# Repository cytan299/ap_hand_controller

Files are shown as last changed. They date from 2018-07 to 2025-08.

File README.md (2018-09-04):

# A simple hand controller for Astro-Physics mounts

by C.Y. Tan 2018

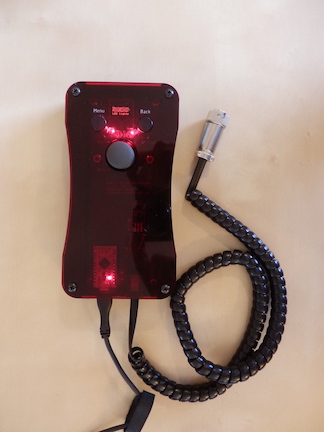
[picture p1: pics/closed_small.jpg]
Simple Astro-Physics Hand controller


It is well-known, that the new GTOCP4 control box can be controlled
with a phone or a pad. However, I really like the feel of real buttons
in a controller rather than using "virtual" buttons on a phone or pad.
This means that the only solution that Astro-Physics (AP) has for people like
me is to buy their AP keypad.

If I had the AP keypad, I will mainly use it for Polar aligning with
PoleMaster and for recalibrating (which is the same as syncing for all
other mounts). After polar alignment and recalibrating, PHD2 will be
used for guiding the scope. Therefore, the AP keypad will only be used
at the start of my imaging session, and no more. Thus, it is hard for
me to justify spending $1000 for an AP keypad when I will hardly use.
I had to figure out a solution.

And here's my solution:
* I have built a simple hand controller for my Mach1GTO. Its purpose
is **not** to replace the AP keypad because it does not initialize the
CP4, have any star database or goto capability etc. My goal is to just
move the mount for calibrating the mount to a star and be compatible
with PoleMaster.

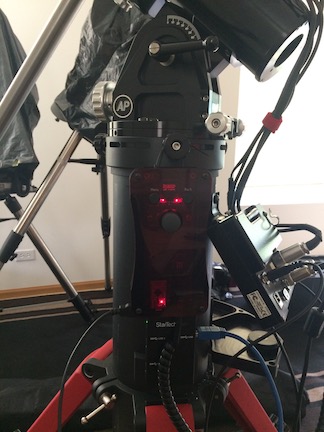
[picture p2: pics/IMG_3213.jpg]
Hand controller connected to the GTOCP4


## Design

The goal of my hand controller is to be low cost (less than $200). The
simplest way I know how to do this is to base it on an
[Arduino controller](https://www.sparkfun.com/products/12640). The
other low cost components are

* A small 64x48
  [OLED display](https://www.ebay.com/itm/0-66-OLED-Display-Module-7pin-64x48-Screen-SPI-I2C-3-3-5V-for-Arduino-AVR-STM32/311968961516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)
  for showing the user options and the state of the controller.
* A [thumb joystick](https://www.sparkfun.com/products/9032) for
selecting menu items and for moving the telescope in RA and DEC.
* The hand controller will be connected to the same port that the AP
  keypad uses. 

## Support

This is unsupported hardware. Build at your own peril! :)

You can submit questions or bug reports using the
[issues](https://github.com/cytan299/ap_hand_controller/issues) tab on
the right and then click on **NEW**.

Have fun!

## Directory structure

* **howto** Assembly instructions for the hand controller.
* **ponoko** The files that are used for laser cutting the acrylic parts of
the design. These files can be sent directly to
[Ponoko](http://www.ponoko.com) for laser cutting.
* **bom** Bill of materials for one hand controller.
* **eagle** Eagle schematic and board files.
* **arduino** Source code for the hand controller.
* **pics** Photographs used in the README's and Wiki.
* **user manual** contains the hand controller user manual.

## Other information

More information can be found in he *README.md* files in each
directory and the [wiki](https://github.com/cytan299/ap_hand_controller/wiki/A-simple-hand-controller-for-Astro-Physics-mounts) of this project on github.

## Copyright
All the software, documentation, and hardware that I have written is
copyright 2018 C.Y. Tan.

All software is released under GPLv3

All documentation is released under:
* Creative Commons Attribution-ShareAlike 3.0 Unported License
* GNU Free Documentation License, Version 1.3
* Creative Commons Attribution-ShareAlike 4.0 International License

All hardware is released under CERN Hardware Open License v1.2

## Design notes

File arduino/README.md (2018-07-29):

# Arduino source code

This directory contains the arduino source code for the hand
controller. The code has been successfully compiled using
ARDUINO 1.8.5.

## Directories

* **hand_controller** This contains the *hand_controller.ino* file
which is the entry point for the controller program.
* **lib** This contains the libraries which are required for compiling
  *hand_controller.ino*. The README.md file contains more information about
  these libraries.

## Copyright

The software that is written by the author is copyright 2018 C.Y. Tan
and released under GPLv3.

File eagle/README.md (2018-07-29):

# Eagle files

These are the eagle files that can be sent to pc board manufacturers to
be made. There is a free version of [eagle](http://cadsoftusa.com)
that can be downloaded to view the designs.

## Directories

* **ap_hand_controller** The hand controller unit schematic and pcb.

## Copyright

The schematic and board designs are copyright 2018 C.Y. Tan and
released under the CERN Open Hardware License v1.2

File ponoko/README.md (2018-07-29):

# Hand controller box and front cover

The hand controller box case and front cover are in this directory. Note that
the svg files are *not* empty! The lines are 0.01 mm thick that are
required for laser cutting by [Ponoko](http://www.ponoko.com). To see
the designs, either zoom in or change the thickness of the lines with
a programme like [Inkscape](https://inkscape.org/en/).

* *ponoko_hc_box_v2.svg* contains enough parts for one hand controller box
and spacers for mounting the pcb into the box. If you use the _red
tint_ acrylic material for this part then you do not need to make a
red, transparent front cover. In my prototype, I had used acrylic
black for the body and
because it is not transparent, I had to make a separate front cover in
red tint. The specified material used for manufacture at [Ponoko](http://www.ponoko.com) is
  * Acrylic red tint or black
  * 3.0 mm thick
  * P2 - 384.0 mm long x 384.0 mm wide
* *ponoko_cover.svg*  is _optional_. It contains the design for the front cover of the
  box.The material used must be red and transparent, i.e.
  * Acrylic red tint
  * 3 mm thick
  * P1 - 181.0 mm long x 181.0 mm wide

## Copyright

The hand controller box and front cover designs are copyright 2018 C.Y. Tan and released under the CERN Open Hardware License v1.2

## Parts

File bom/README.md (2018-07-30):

# Bill of Materials

The estimated cost for building *one* hand controller is about $150.
Taxes and shipping have not been included. This is the lower bound for
the cost of one such device because, in practise, it is not possible
to just buy 1 screw.  The bom.ods file is readable using
[LibreOffice Calc](http://www.libreoffice.org).

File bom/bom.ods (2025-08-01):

Part # | Description | Price each | # required | Cost of 1 | Bought from | Total cost of 1
COM-00589 | RS232 converter SMD | $1.95 | 1 | $1.95 | www.sparkfun.com | $156.86
COM-09032 | Thumb Joystick | $3.95 | 1 | $3.95
COM-10302 | Tactile Button Assortment | $0.50 | 2 | $0.99
DEV-12587 | Pro Micro - 3.3V/8MHz | $19.95 | 1 | $19.95
PRT-00132 | RJ11 6-Pin Connector | $1.25 | 1 | $1.25
ROB-13134 | Standoff 6-32, 1” | $0.62 | 4 | $2.49
450-1661-ND | Tactile switch right angled | $0.18 | 1 | $0.18 | www.digikey.com
945-1661-5-ND | R-78E3.3-0.5 DC/DC converter 3.3V | $2.70 | 1 | $2.70
HR1732-ND | Connector plus male 5 position | $13.49 | 1 | $13.49
A3662R-05C-ND | Cable mod 6P6C plug cable 5 ft | $3.13 | 1 | $3.13
160-1169-1-ND | LED green 1206 SMD | $0.25 | 1 | $0.25
160-1406-1-ND | LED yellow 1206 SMD | $0.28 | 1 | $0.28
 | PCBs | $22.00 | 1 | $22.00 | www.oshpark.com
10792 | 64x48 0.66” OLED white display module | $4.90 | 1 | $4.90 | https://www.buydisplay.com/serial-spi-i2c-white-0-66-inch-arduino-raspberry-pi-oled-display-64x48
331712 | Laser cut case | $59.30 | 1 | $59.30 | www.ponoko.com
99558 | 6-32 3/8” black pan head screws | $0.30 | 8 | $2.40 | www.homedepot.com
99388 | 4-40 1/2” black pan head screws | $0.29 | 6 | $1.74
887480021219 | 4-40 nuts | $0.10 | 6 | $0.59
 | Taxes | $0.56
C503B-RAN-CZ0C0AA2 | Red clear 5 mm round LED | $0.15 | 2 | $0.30 | www.digikey.com
RHM100AHTR-ND | 0805 surface mount 100 ohm resistor | $0.36 | 2 | $0.72
732-8086-2-ND | 1206 surface mount 0.1 uF ceramic capacitor | $0.10 | 5 | $0.50
1189-4041-ND | Radial electrolytic capacitor 10uF, 50V | $0.28 | 2 | $0.56
10.0KXBK-ND | 10 kohm resistor, ¼ W | $0.10 | 4 | $0.40
49.9XBK-ND | 50 ohm, ¼ W | $0.10 | 1 | $0.10
ED3024-ND | 24 pin IC socket | $1.12 | 1 | $1.12
ED4624-ND | 24 pin IC wirewrap socket | $4.66 | 1 | $4.66
3008 | 36-pin 0.1” short female header | $1.60 | 0.194 | $0.31 | www.adafruit.com
MMPin-40 | 40 pin SIP header strip | $2.66 | 1 | $2.66 | www.solarbotics.com
 | Olympus adjustable wrist wrap | $3.99 | 1 | $3.99 | https://www.amazon.com/gp/product/B001TKYMTA/ref=oh_aui_detailpage_o00_s00?ie=UTF8&psc=1

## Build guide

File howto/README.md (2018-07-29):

# How to build the AP hand controller

I have written one document to help you build and assemble my AP hand controller

## The documents

* **assembly.pdf** This guide tells you how I assembled the
  parts of hand controller.

## Copyright

These documents are copyright 2018 C.Y. Tan and released under
Creative Commons Attribution-ShareAlike 3.0 Unported License.

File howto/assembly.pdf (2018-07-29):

# AP handcontroller assembly instructions

## C.Y. Tan

7/29/18

2 | AP Handcontroller | 7/29/18

# License

## Copyright 2018 C.Y. Tan This document is licensed under Creative Commons Attribution-ShareAlike 3.0 Unported License. To view a copy of this license, visit http://creativecommons.org/licenses/by-sa/3.0/

3 | AP Handcontroller | 7/29/18

# Assembly instructions

## - These instructions will only highlight the important parts of the

assembly.

### - The assembly is quite straightforward, but as usual, there are some parts of

the assembly that need a little bit of care and feeding.
- All the required parts are listed in the bill of materials.

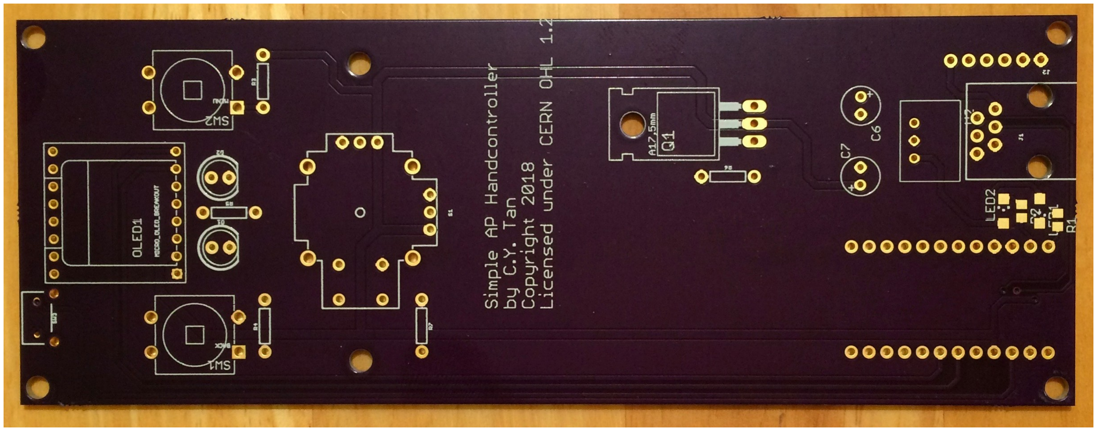
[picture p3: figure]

4 | AP Handcontroller | 7/29/18

# Electronics

This is the prototype printed circuit board that I’ll be using to demonstrate how to assemble the hand controller.

The version 2 hand controller that is on the github site is nearly the same as the prototype. The obvious part that is missing in version 2 of the hand controller is the MOSFET.

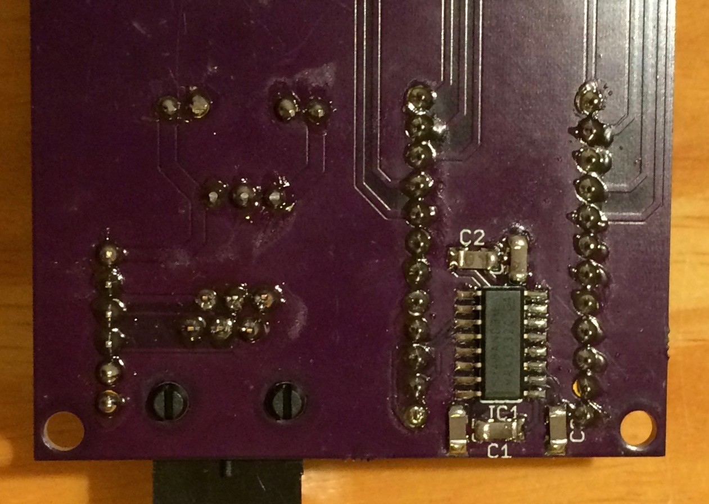
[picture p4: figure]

5 | AP Handcontroller | 7/29/18

# Surface mount parts

There are surface mount parts that need to be soldered at the back of the printed circuit board.

These parts are for the RS232 level shifters. They are actually very easy to solder to the pads with thin solder (0.8 mm diameter, 60/40 solder) and a soldering iron with a fine tip.

However, if you’ve never soldered before, it’s best to ask a friend who is an experienced at soldering electronics to do it.

# Making the pushbuttons

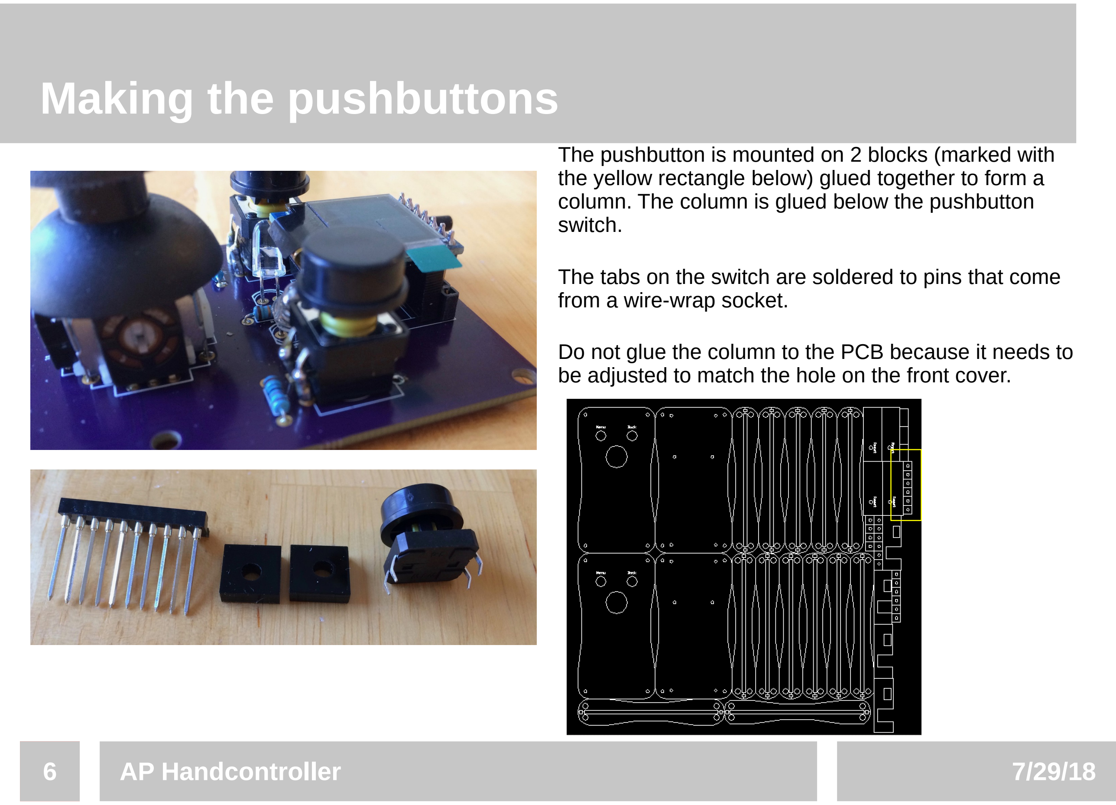
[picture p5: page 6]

6 | AP Handcontroller | 7/29/18

The pushbutton is mounted on 2 blocks (marked with the yellow rectangle below) glued together to form a column. The column is glued below the pushbutton switch.

The tabs on the switch are soldered to pins that come from a wire-wrap socket.

Do not glue the column to the PCB because it needs to be adjusted to match the hole on the front cover.

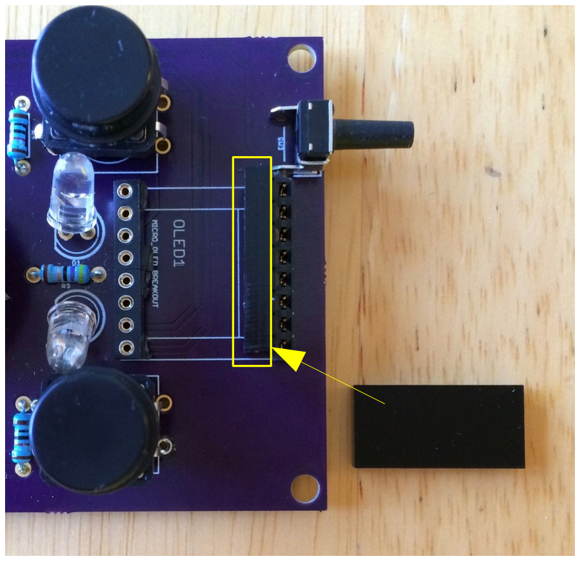
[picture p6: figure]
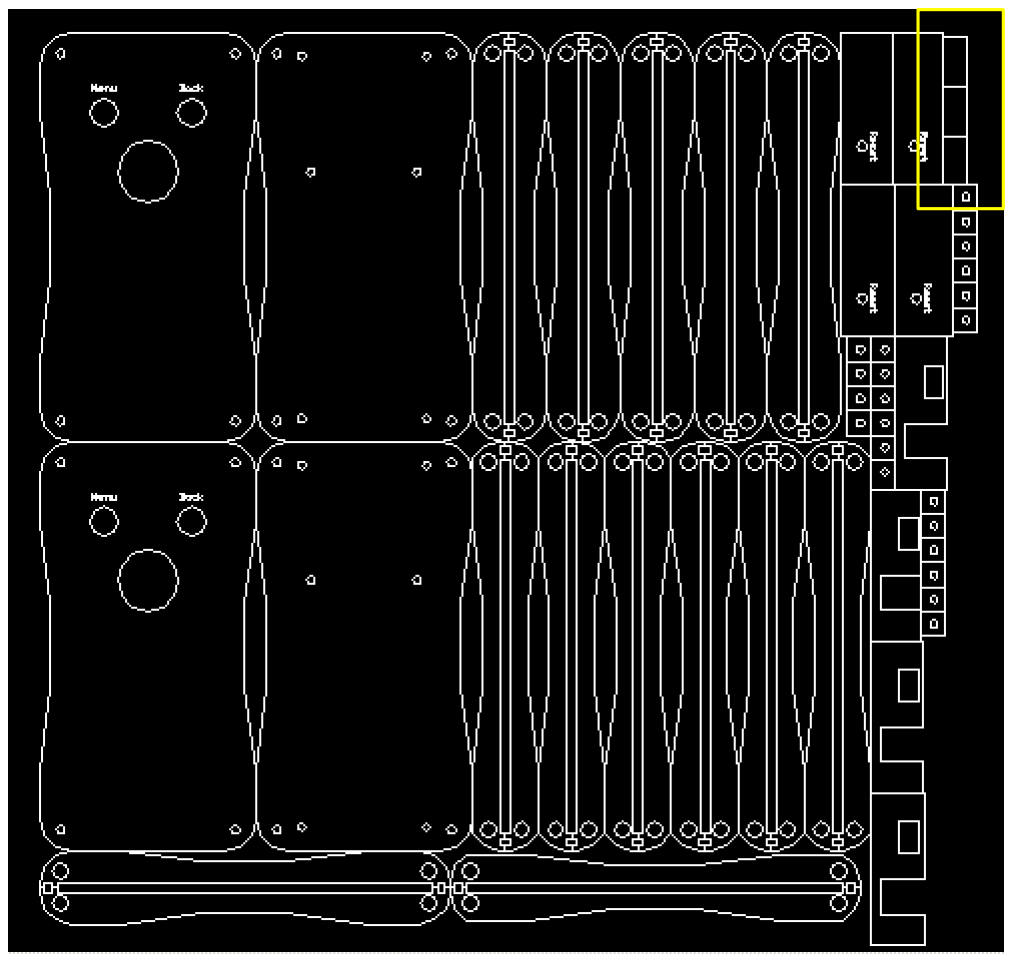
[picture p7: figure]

7 | AP Handcontroller | 7/29/18

# Supporting the OLED

The OLED module only has pins on one side and so it flops after installation into its socket. There are blocks (marked in a yellow rectangle in the right figure) that can be used to prop up the OLED. The block is simply glued to the PCB.

Note: The above PCB is the prototype version. Version 2 has the OLED socket nearest to the LEDs.

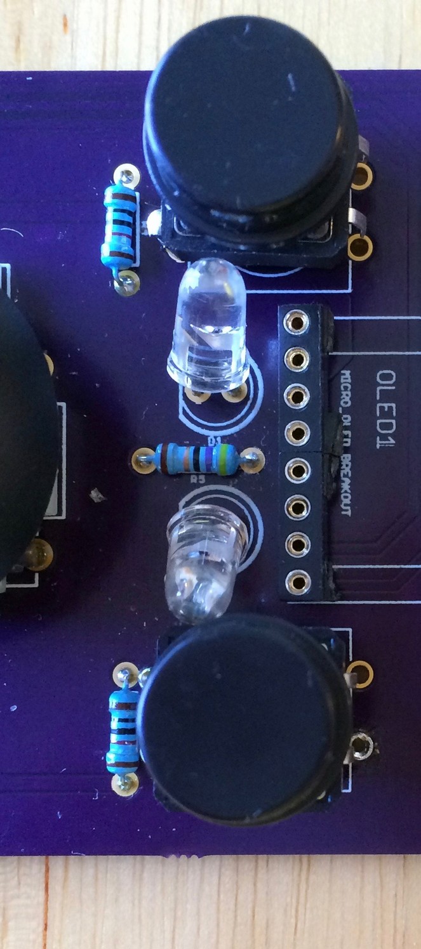
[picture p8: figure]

8 | AP Handcontroller | 7/29/18

# Installation of LEDs

The LEDs are used to light up the switches so that they can be seen in the dark.

They are bent towards the switches and should be installed last.

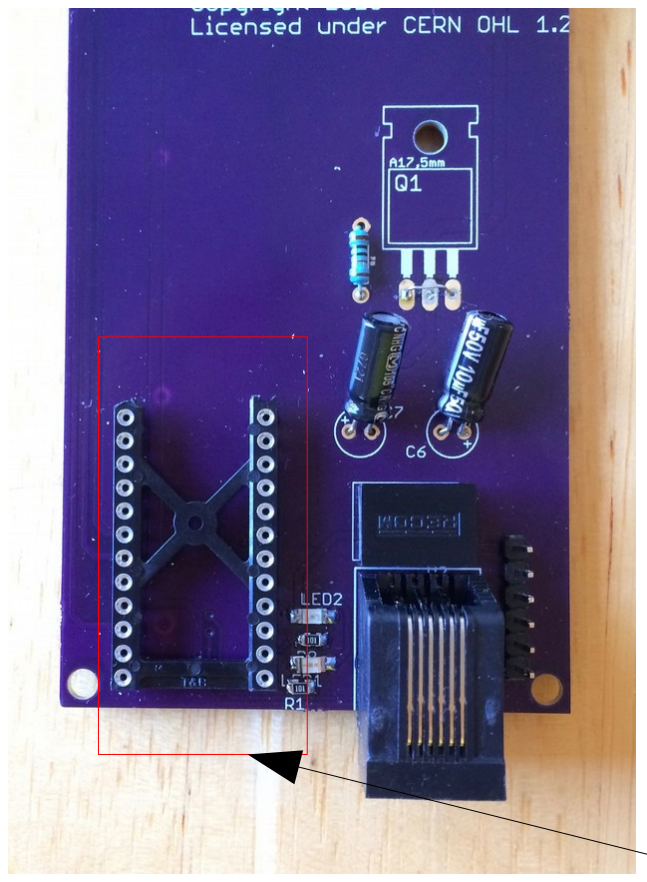
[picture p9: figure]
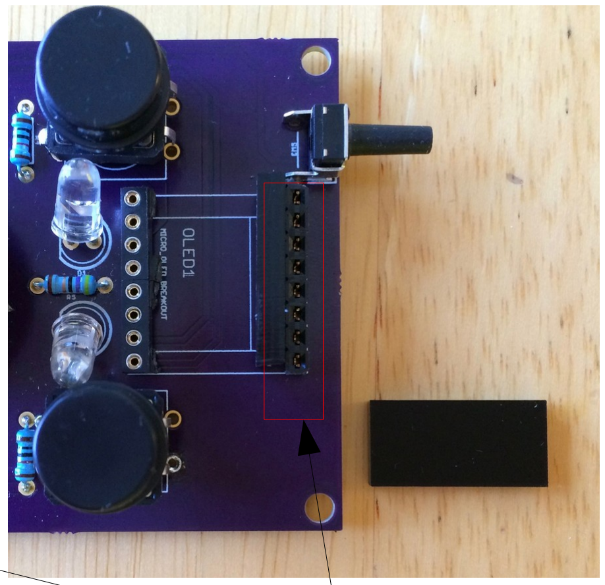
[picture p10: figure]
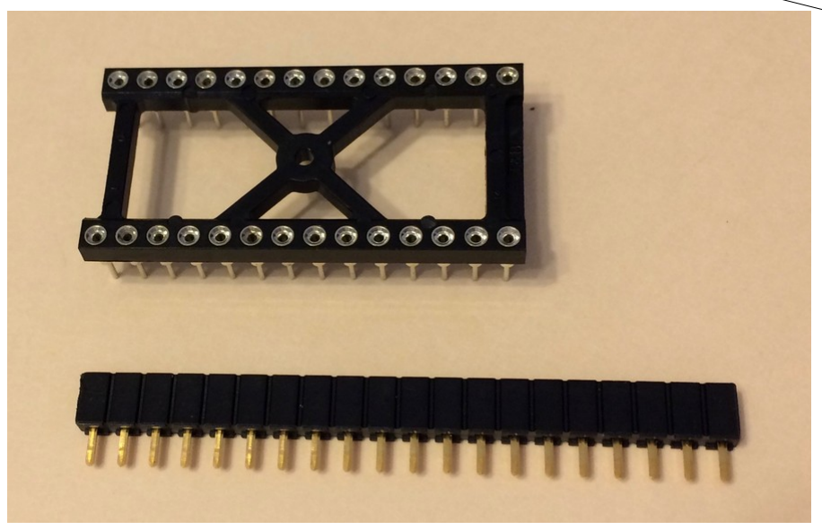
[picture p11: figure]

9 | AP Handcontroller | 7/29/18

# Populating the PCB

Populate the lowest height components first. Start with surface mount parts, and then resistors, IC sockets, electroytic capacitors, switches, 6P6C connector and finally the joystick.

The assembly of the pushbuttons and LEDs are discussed in later slides.

Sockets are used for the Arduino and the OLED display.

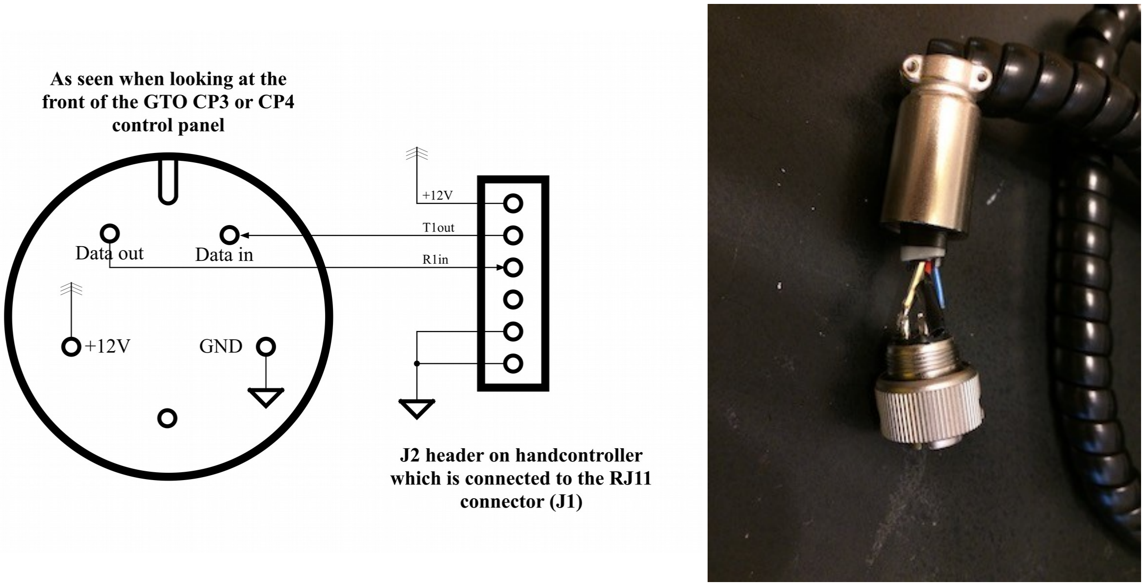
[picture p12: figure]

10 | AP Handcontroller | 7/29/18

# Making the AP keypad connector

There are 6 wires but only 5 wires are soldered to the connector. The 2 GND wires are soldered to the same pin.
One of the extra wires is just covered with insulating tape.

# Making the case

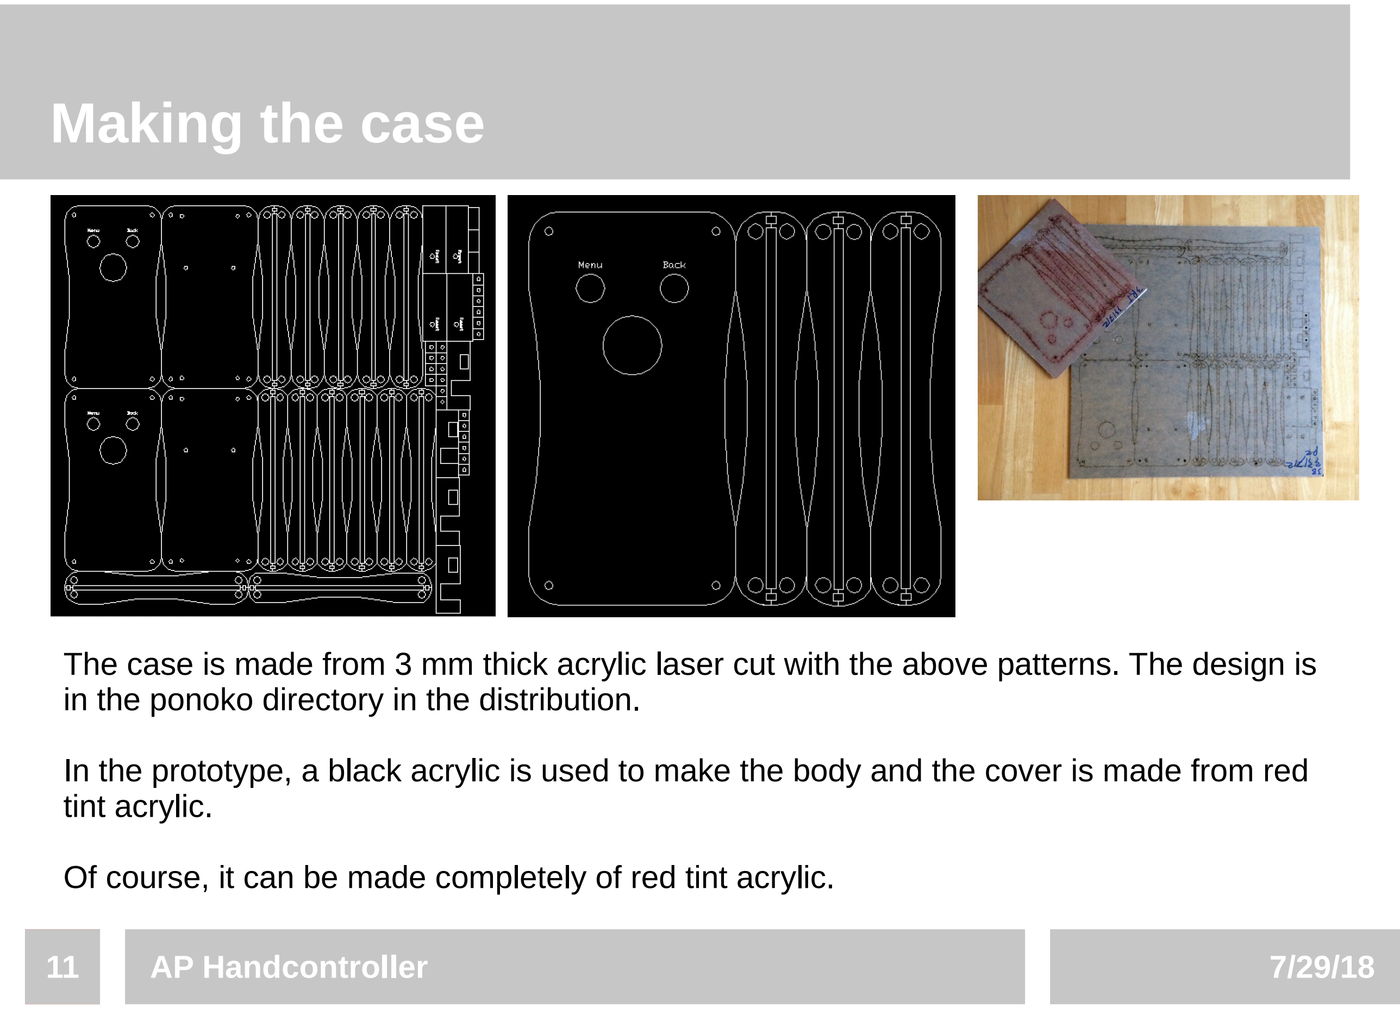
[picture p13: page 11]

11 | AP Handcontroller | 7/29/18

The case is made from 3 mm thick acrylic laser cut with the above patterns. The design is in the ponoko directory in the distribution.

In the prototype, a black acrylic is used to make the body and the cover is made from red tint acrylic.

Of course, it can be made completely of red tint acrylic.

# Stacking the case

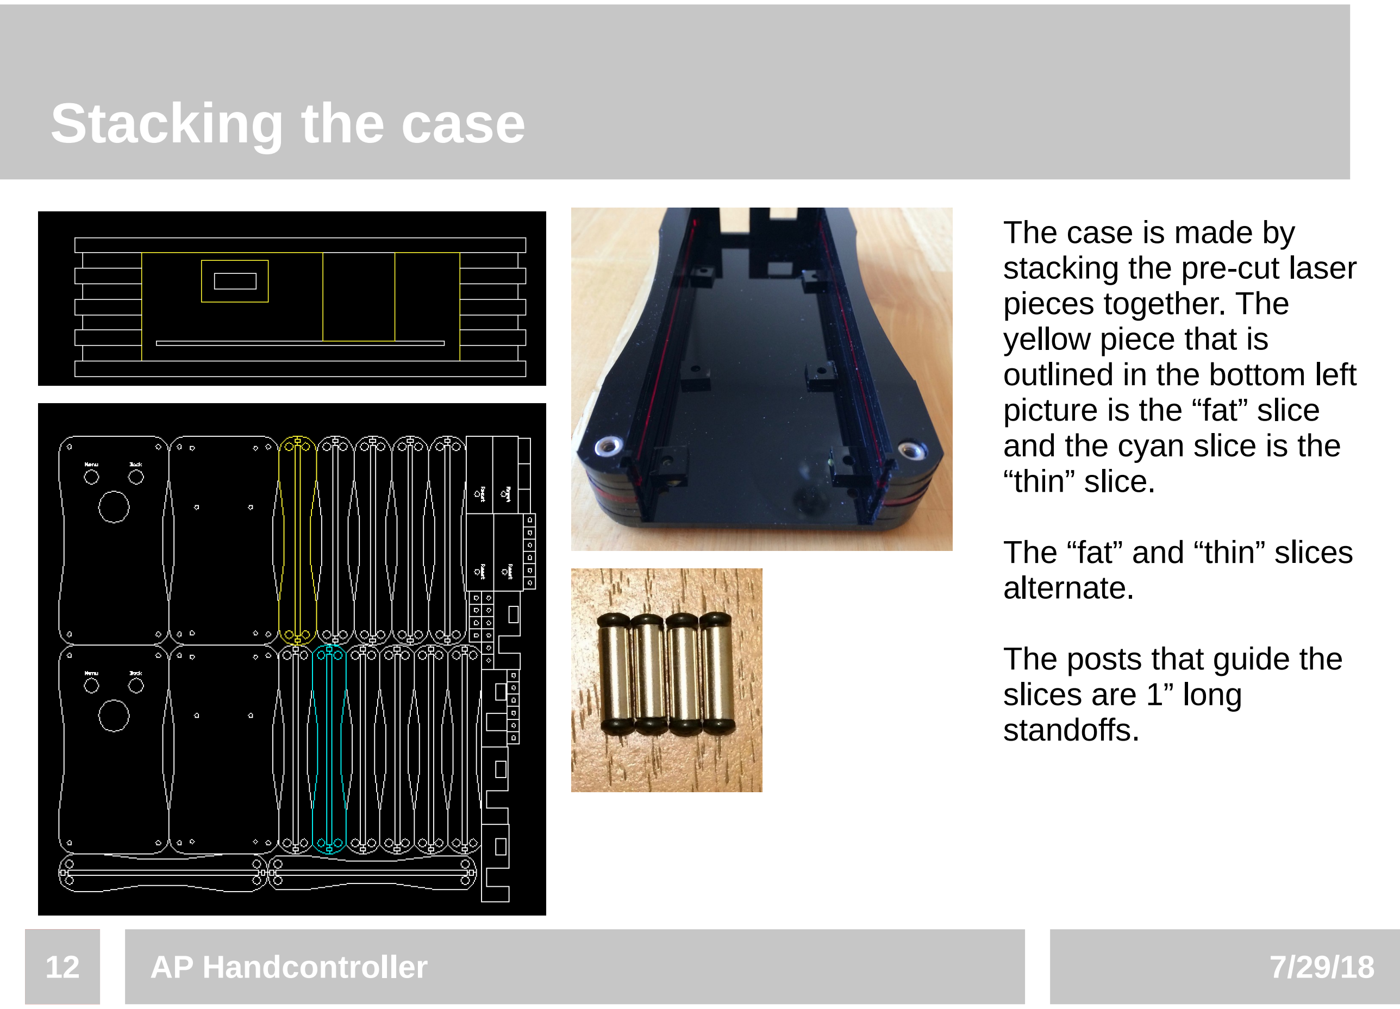
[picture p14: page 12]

12 | AP Handcontroller | 7/29/18

The case is made by
stacking the pre-cut laser pieces together. The
yellow piece that is
outlined in the bottom left picture is the “fat” slice and the cyan slice is the
“thin” slice.

The “fat” and “thin” slices alternate.

The posts that guide the
slices are 1” long
standoffs.

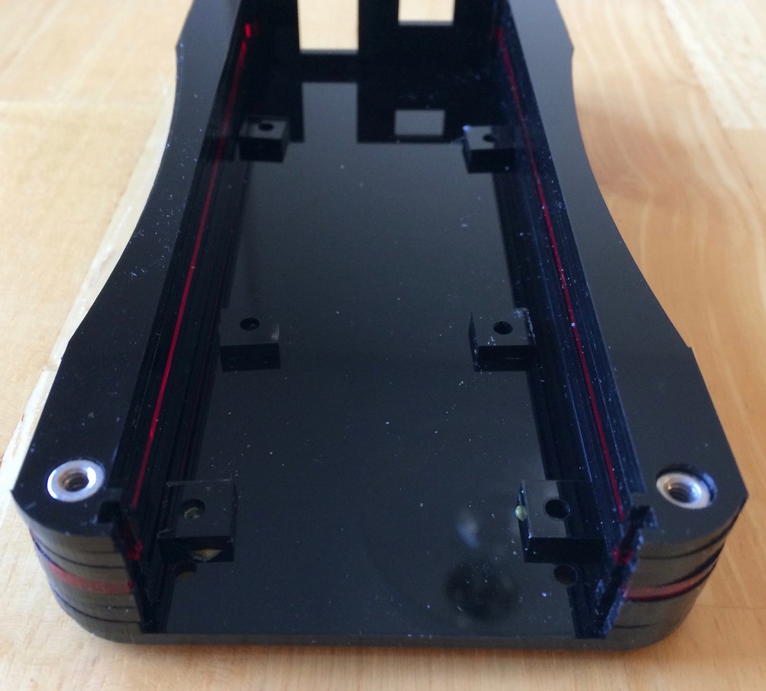
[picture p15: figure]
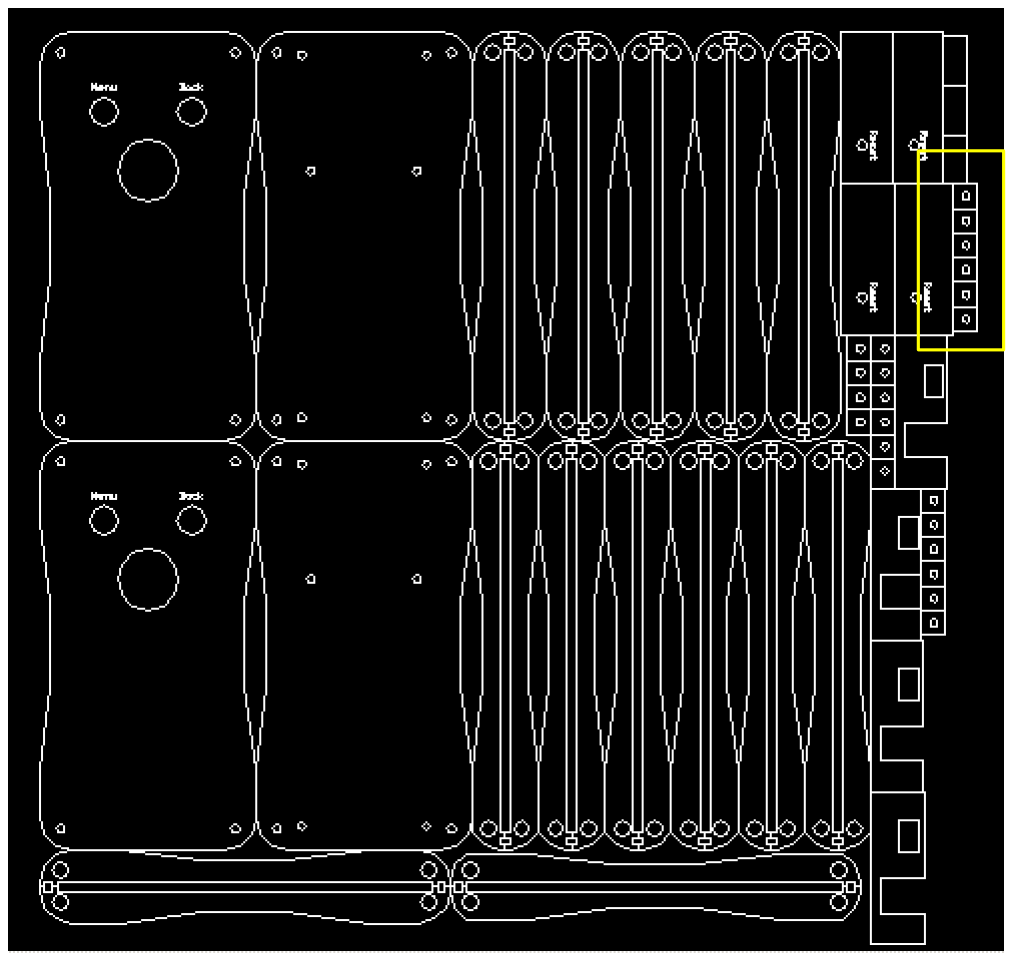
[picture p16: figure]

13 | AP Handcontroller | 7/29/18

# Gluing in standoffs

The blocks that are used to make standoffs are in the yellow rectangle in the right figure. They are glued to the bottom of the case.

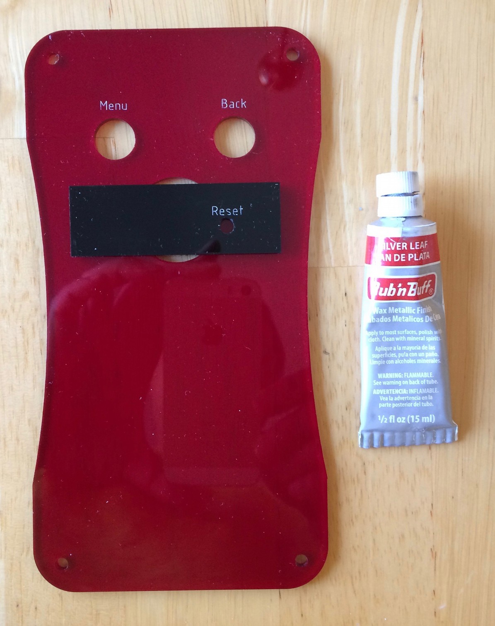
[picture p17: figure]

14 | AP Handcontroller | 7/29/18

# Highlighting marks

The laser engraved characters are highlighted by rubbing in silver Rub’N’Buff compound.

The excess is wiped off using ethanol.

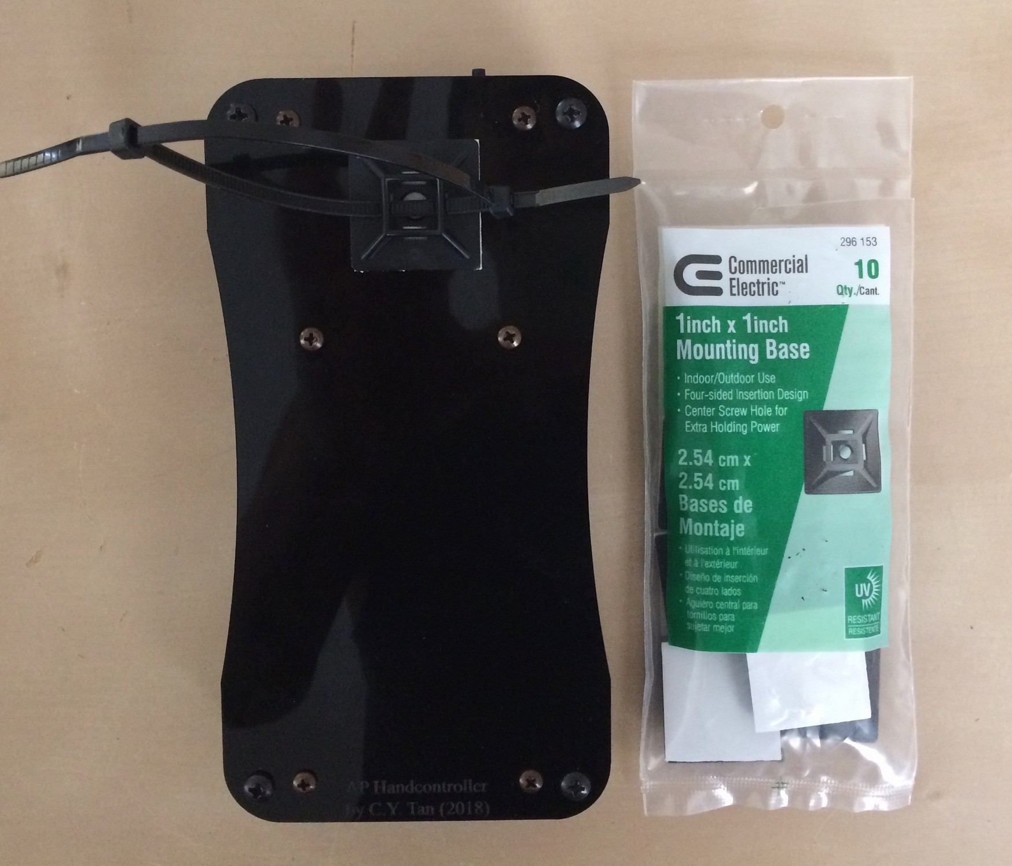
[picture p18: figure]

15 | AP Handcontroller | 7/29/18

# Hanging loop for the controller

I made a hanging loop for the controller using cable ties looped through a cable tie mounting base.

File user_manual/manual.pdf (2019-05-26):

# A Simple Hand Controller for Astro-Physics

Mounts Operating Manual by C.Y. Tan (26.

# May. 2019)

## 1 License

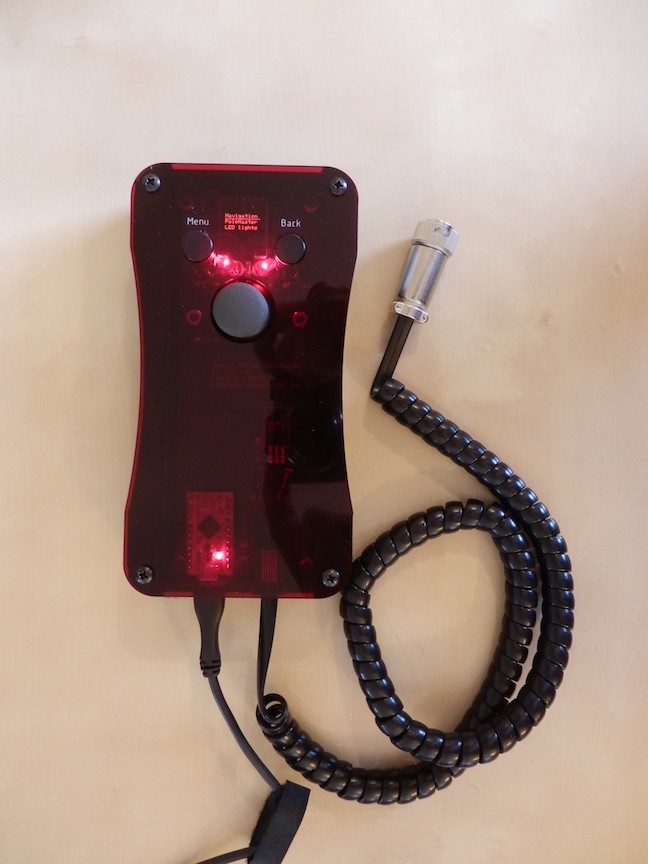
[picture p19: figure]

This work is licensed under the Creative Commons Attribution-ShareAlike 4.0 International License. To view a copy of this license, visit http://creativecommons.org/licenses/by-sa/4.0/ or send a letter to Creative Commons, PO Box 1866, Mountain View, CA 94042, USA.

## 2 Introduction

It is well-known, that the new GTOCP4 control box can be controlled with a phone or a pad. However, I really like the feel of real buttons in a controller rather than using “virtual” buttons on a phone or pad. This means that the only solution that Astro-Physics (AP) has for people like me is to buy their AP keypad.

If I had the AP keypad, I will mainly use it for Polar aligning with PoleMaster (lately with SharpCap

A Simple Hand Controller for Astro-Physics Mounts Operating Manual | 1

Pro as well) and for recalibrating (which is the same as syncing for all other mounts). After polar alignment and recalibrating, PHD2 will be used for guiding the scope. Therefore, the AP keypad will only be used at the start of my imaging session, and no more. Thus, it is hard for me to justify spending $1000 for an AP keypad which I will hardly use.

I had to figure out a solution.

And here's my solution:
- I have built a simple hand controller for my Mach1GTO. Its purpose is not to replace the AP keypad because it does not initialize the GTOCP4, have any star database or goto capability etc. My goal is to just move the mount for calibrating the mount to a star and be compatible with PoleMaster.

## 3 The hand controller hardware guide

The hand controller plugs into the GTOCP3 or GTOCP4 keypad port.

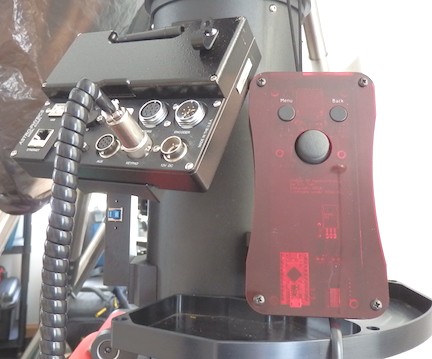
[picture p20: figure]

The hand controller does NOT have the RECAL option. This is a deliberate design decision. This is so that there will never be any confusion about which device will RECAL – it will always be the computer that is connected to the mount.

## 3.1 The buttons and joystick action guide

The actions associated with the buttons and joystick are defined in the table shown below. The shortcuts for that are used in this manual are also defined here.

A Simple Hand Controller for Astro-Physics Mounts Operating Manual | 2

Button | Description | Shortcut
Menu | When pressed, the hand controller goes back to the main menu. It also
| stops the mount from slewing. | MENU
Back | When pressed, the hand controller goes back to the previous menu. It
| also stops the mount from slewing. | BACK
Reset | Resets the hand controller. | RESET
Joystick UP/DOWN | In the menu environment, UP/DOWN, moves the cursor up and down. In the navigation environment, UP/DOWN is mapped to North/South slews. | ⇧/⇩
Joystick LEFT/RIGHT | In the menu environment, LEFT/RIGHT acts like a swipe. RIGHT moves to the next selected submenu. LEFT goes back to the previous menu. In the navigation environment, LEFT/RIGHT is mapped to East/West slews. | ⇦ ⇨/
Joystick Button | In the menu environment, the joystick button acts like the return key. In the navigation environment, the joystick button cycles through the slew rates. | ◙

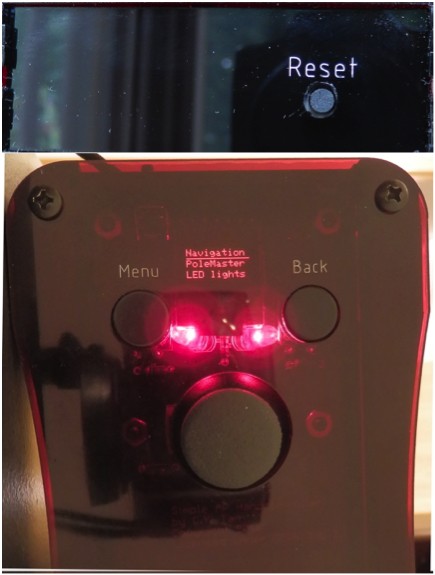
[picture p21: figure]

A Simple Hand Controller for Astro-Physics Mounts Operating Manual | 3

## 4 How to use

The hand controller can be connected to the GTOCP3 or GTOCP4 keypad port before power up. If it is
connected before power up, the controller has to be | RESET | before use. This is to establish a reliable
serial connection with the mount. IMPORTANT! The mount must be unparked (in APCC or the AP
ASCOM driver) and | RESET | must be pushed before use. If you use the hand controller before the
mount is unparked, the hand controller will still move the mount but POLEMASTER::SET HOME will be incorrect and thus POLEMASTER::GO HOME will send the mount to the wrong position.
Once powered up and | RESET | you can start using the hand controller.

## 4.1 Menu actions

Everything starts from the Main Menu.

Move through each menu item by ⇧/⇩,
and select it with ◙, or use . ⇨
In order to get back out of any control panel or submenu, just use | MENU | or use | BACK.
Pressing these buttons also stops the mount from moving. This is one way to stop the mount if anything goes wrong during a slew.
A Simple Hand Controller for Astro-Physics Mounts Operating Manual | 4

### 4.1.1 Navigation menu

Selecting Navigation brings up the Navigation submenu which has 3 submenu items.

Selecting the Navigate menu brings up the control panel that allows the user to move the mount. | This panel allows the user to move the mount. The slew rate is cycled with ◙. The numbers represent the slew rate, 0: stopped, 1: 12x, 2: 64x, 3: 600x, 4: 1200x.
Selecting the ???_???x menu brings up the slew speed menu. ???_???x displays the current default slew speed. | Use ◙ to cycle through the slew rates. Possible rates are: Fine_12x, Slow_64x, Med_600x and Fast_1200x.
Move the mount with proportional control using Prop Nav. The slew rate depends on the position of the joystick. | As the joystick is pushed from its home position, the slew rate starts from 12x, 64x, 600x and then finally 1200x at its maximum position.
A Simple Hand Controller for Astro-Physics Mounts Operating Manual | 5

### 4.1.2 PoleMaster menu

The PoleMaster menu items makes the hand controller compatible with the calibration routine of PoleMaster or SharpCap Pro. The three menu items are the sequence of actions that the
PoleMaster calibration routine will go through during Polar alignment. IMPORTANT! | RESET | must
be pushed after the mount is UNPARKED (in APCC or the AP ASCOM driver) before the actions of this menu can work properly.

Selecting PoleMaster brings up the submenu items designed for ease of use with the
PoleMaster calibration routine.

Select the Set home menu item to remember the position of the mount before the start of the PoleMaster calibration routine.

The RA move menu item brings up the control panel for moving the telescope in RA at 1200x speed. | In this control panel, the mount can only move in RA, i.e. East or West at full speed at 1200x.

Selecting Go home moves the mount back to the position that was selected by Set home.

A Simple Hand Controller for Astro-Physics Mounts Operating Manual | 6

### 4.1.3 LED lights menu

Selecting LED lights brings up the control panel for adjusting the brightness of the LEDs that
illuminate the | Menu | and | Back | buttons.

Use ⇦ ⇨/ to set the brightness of the LEDs.

## 5 Support

As usual, for any open source project, you build and use the hand controller at your own risk. No warranty is implied.

However, questions can be submitted to issues, (https://github.com/cytan299/ap_hand_controller/issues) but answers to questions are again not guaranteed.

A Simple Hand Controller for Astro-Physics Mounts Operating Manual | 7

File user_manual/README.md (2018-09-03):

# User manual

The user manual for the hand controller is here.

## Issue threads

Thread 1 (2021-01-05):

Digi-Key part numbers for lines 22 to 26 of the AP Hand Controller Parts List

ab15Kath, 2021-01-05:
Attn. cytan,
Could you kindly provide a Part # for the following lines of your bill of materials list:
LINE 22: 	0805 surface mount 100 ohm resistor
LINE 23:  	1206 surface mount 0.1 uF ceramic capacitor
LINE 24:	Axial electrolytic capacitor 10uF, 50V
LINE 25:	10 kohm resistor, ¼ W
LINE 26:	50 ohm, ¼ W
Thanks,
Andrew
abrenyo@rogers.com

cytan299, 2021-01-06:
Hi Andrew,
   The above parts are really generic. Any vendor will do on Digikey. I bought surface mount, caps and resistor kits and selected the parts out from my kits, so I don't have any part numbers.

   So are you planning to build the hand controller?

cytan

ab15Kath, 2021-01-06:
Hi cytan,Thank you for responding!Yes, I am buying the parts as we email.I  like the hand held feeling of a controller rather than a mobile phone.I am not very good at electronics but I had a good look at all the work you did in providing excellent directions and material so I am confident in assembling the controller.I would really appreciate it if you wouldn't mind picking the generic parts for me to make it fool proof for me - I have never selected electronic parts before and my order is stalled at those parts. There are something like a few thousand choices for one item alone. I don't know what to select. I hope that it's not too much work.The rest has all been ordered.I am really looking forward to this project as there are isn't much stargazing with the weather in Ontario, Canada.Many thanks for your design - I have an AP1100 as my retirement endeavour and I am slowly building my setup over a few years.Andrew Brenyo

Sent from Rogers Yahoo Mail on Android

  On Tue, Jan 5, 2021 at 9:33 PM, cytan299<notifications@github.com> wrote:

Hi Andrew,
The above parts are really generic. Any vendor will do on Digikey. I bought surface mount, caps and resistor kits and selected the parts out from my kits, so I don't have any part numbers.

So are you planning to build the hand controller?

cytan

—
You are receiving this because you authored the thread.
Reply to this email directly, view it on GitHub, or unsubscribe.

cytan299, 2021-01-06:
I'll send you the part numbers tomorrow.

cytan299, 2021-01-07:
I've updated the BOM to include the missing Digikey part numbers.

Also, FYI, I use the hand controller with both my AP1100AE and Mach1GTO and it works great with PoleMaster or SharpCap for Polar Alignment.

ab15Kath, 2021-01-07:
Hi cytan,

Fantastic, thank you so much for your help. I will finish my order tonight and hopefully put it together in a few weeks once all the parts are in.

I will also keep in mind using PoleMaster or SharpCap for Polar Alignment once I get there.

A Happy New Year to you and your family and a safe 2021,

Andrew Brenyo

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

Closed 2021-01-07.

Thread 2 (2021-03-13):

Power-up issue

ab15Kath, 2021-03-13:
Hi C.Y.Tan,

The Simple A-P Hand Controller that you designed is wonderful. I really like the in-the-hand feel and the fine control of the thumb joystick.
Now that I have built the hand controller I am truly amazed by all the work you put into it!
I have only one issue to get it fully functional. I cannot get it to power-on once I plug it into the GTOCP4 box. The yellow LED2 turns on and stays on, but the SparkFun Pro Micro power LED does not light up or the OLED. However, once I connect a micro USB to the Pro Micro board the power LED lights up and I am able to move my GTO1100 mount. The yellow LED2 turns off when the micro USB is used to power the hand controller PCB.
Is it a hardware or software problem? I triple checked all of my soldered connections and your Sketch loaded from Arduino flawlessly. I connected the hand controller PCB to a 12 volt battery and, once again, only the yellow LED2 would light up and stay on. What am I not understanding – do I need to initialize/turn on something on the mount? I have no PCB programming experience.
I am completely stumped as to how to power-up the hand controller from the mount. I would appreciate any help that you can provide.
Here is my setup:
1.	The dedicated power source for the mount is a Pyramid 12 Volt DC converter.
2.	I use APCC to control my mount, firmware version VCP4-P02-08 (latest version).
3.	I installed the SparkFun drivers to Arduino prior to loading the sketch.
4.	I use RASPA for polar alignment, but I would like to learn how to use PoleMaster.
5.	I’ve included four photos of the PCB - just in case some hardware is missing.

Thanks,
Andrew Brenyo
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

cytan299, 2021-03-13:
Thanks for your kind words.

Since everything works when powered via the USB port, this means that when you connect the hand controller to CP4, it's not getting power.

You'll need to check the following with a voltmeter

1.  12 V is getting into the board after you plug it into the CP4. Check pin 1 of the J2 header. It should read 12 V. If it doesn't read 12 V, the cable that you made is not correct. See slide 10. Make sure the 12 V wire is soldered to the connector.
2. Check that 3.3 V regulator (U2) is spitting out 3.3V. There are 3 pins on the regulator (R78E3.3), one of them should be 12 V, the middle one is ground and the other should be 3.3 V.
3. Finally, the arduino Pro Micro should see 3.3V. Check pin 21 of the Pro Micro. If it is not 3.3V then there could be an open between the Pro Micro and the regulator.

My bet is that you didn't wire the cable that connects the CP4 to the controller correctly. Post a followup whether that's the problem or not.

cytan

ab15Kath, 2021-03-27:
Hi cytan,

I followed through on your suggestions and was able to power-up the hand controller from the mount.
However, the solution turned out to be something completely unexpected – at least from my novice point of view.
1.	I checked Pin 6 (12VIN) of the J2 header and Pin 1 (GND) and had a reading of 13.74 volts using a voltmeter. So the PCB was getting enough power.
2.	The 3.3V regulator was working fine too, with the IN side showing a reading above 12 volts and the OUT side showing a reading of 3.28 volts.
3.	Your suggestion to check Pin 21 (VCC) was a good idea, it only read ~1.27 volts. There may be an opening/break from the R2 to the Max3232CSE chip, but I have not checked that far yet.
Photo 3630: Hand Controller PCB turned on and fully functional with power from the mount – all commands work properly.
Photo 7888: Jumper cable from LED 2 (positive side) to Pin 21 (VCC). The hand controller powered-up fully once connected to the mount using this wiring.
Photo 2356: Showing the orientation of the LEDs. Both were checked with a 3.5 volt battery pack and lit up properly. I checked the 1000 resistors at either end of their connections and, once again, the LEDs lit up. Confirming the connections are good. Don’t mind the messy connections I did a re-solder of many of the components just in case there was a poor connection somewhere.
Photo 5299: The CP4 connector with the wires matching Slide 10. Again, the wiring is a bit messy as I tried different combinations. I tried the connector without the yellow wire soldered and then with only the green wire soldered to see if it would make a difference and had no success.
The jumper wiring was a surprise as I tested each connection, and although it works, I would appreciate a better or possibly the correct wiring solution. I am a bit concerned that I will burn out or melt my board by bypassing R2. With my lack of experience I’m afraid that I might fry the Pro Micro board if I try too many solutions.

Thanks,
Andrew
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

Closed 2021-03-27.

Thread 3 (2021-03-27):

A big thanks!

ab15Kath, 2021-03-27:
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
I've attached a photo of the finished hand controller. I went with a white case to match equipment and I prefer white at night with my glasses. If I may suggest, after looking at previous versions of your PCB, that it appears the source of the previous power issue was the connection between C7 and the East side of the thumb joystick. I think once the MOSFET was removed the power strip needed to stay in place to complete the circuit. I used the hand controller recently to image M42 & M43 and it was a joy to use. Once again, I thank you for your excellent AP Hand Controller design. Andrew    As a final note I've included the M42 & M43 image - so much easier to frame using your hand controller.

cytan299, 2021-03-27:
Hi Andrew,
   A big thanks for finding the wiring bug! I've corrected the PCB and will upload it later.  I believe you're the first person to build my hand controller and that's why the bug was not discovered until now.
   As for the hand controller, I use mine all the time, during every imaging session to Polar Align. I hope it'll work for you as well as for me.

cytan

Closed 2021-04-03.

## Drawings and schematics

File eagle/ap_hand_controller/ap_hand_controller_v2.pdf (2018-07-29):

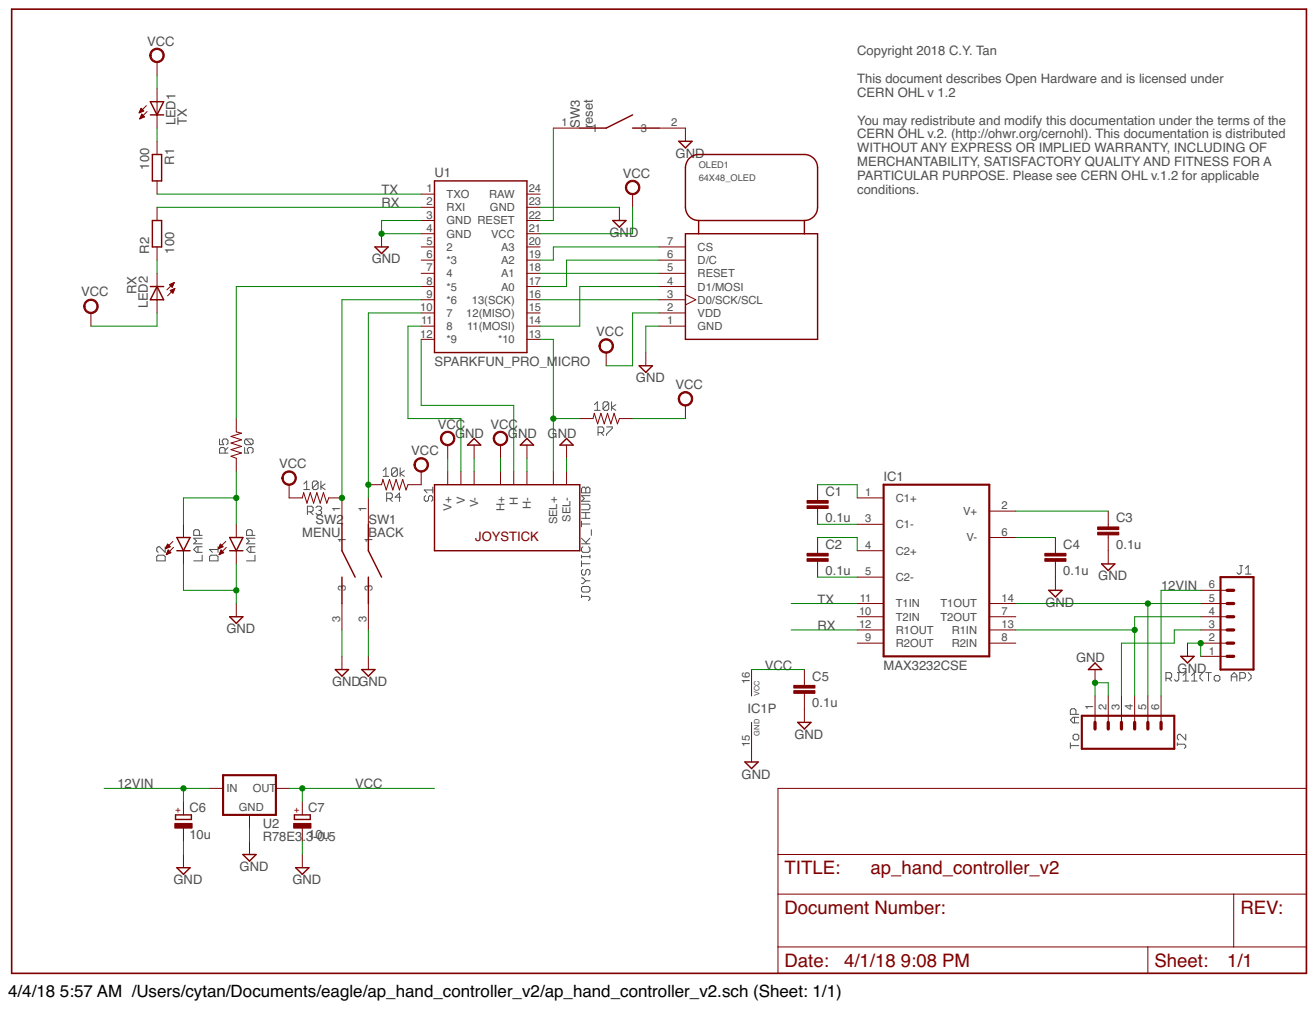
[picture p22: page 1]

Copyright 2018 C.Y. Tan This document describes Open Hardware and is licensed under CERN OHL v 1.2

You may redistribute and modify this documentation under the terms of the CERN OHL v.2. (http://ohwr.org/cernohl). This documentation is distributed

WITHOUT ANY EXPRESS OR IMPLIED WARRANTY, INCLUDING OF
MERCHANTABILITY, SATISFACTORY QUALITY AND FITNESS FOR A
PARTICULAR PURPOSE. Please see CERN OHL v.1.2 for applicable
conditions.

Document Number: | REV:

Date: 4/1/18 9:08 PM | Sheet: 1/1

4/4/18 5:57 AM /Users/cytan/Documents/eagle/ap_hand_controller_v2/ap_hand_controller_v2.sch (Sheet: 1/1)

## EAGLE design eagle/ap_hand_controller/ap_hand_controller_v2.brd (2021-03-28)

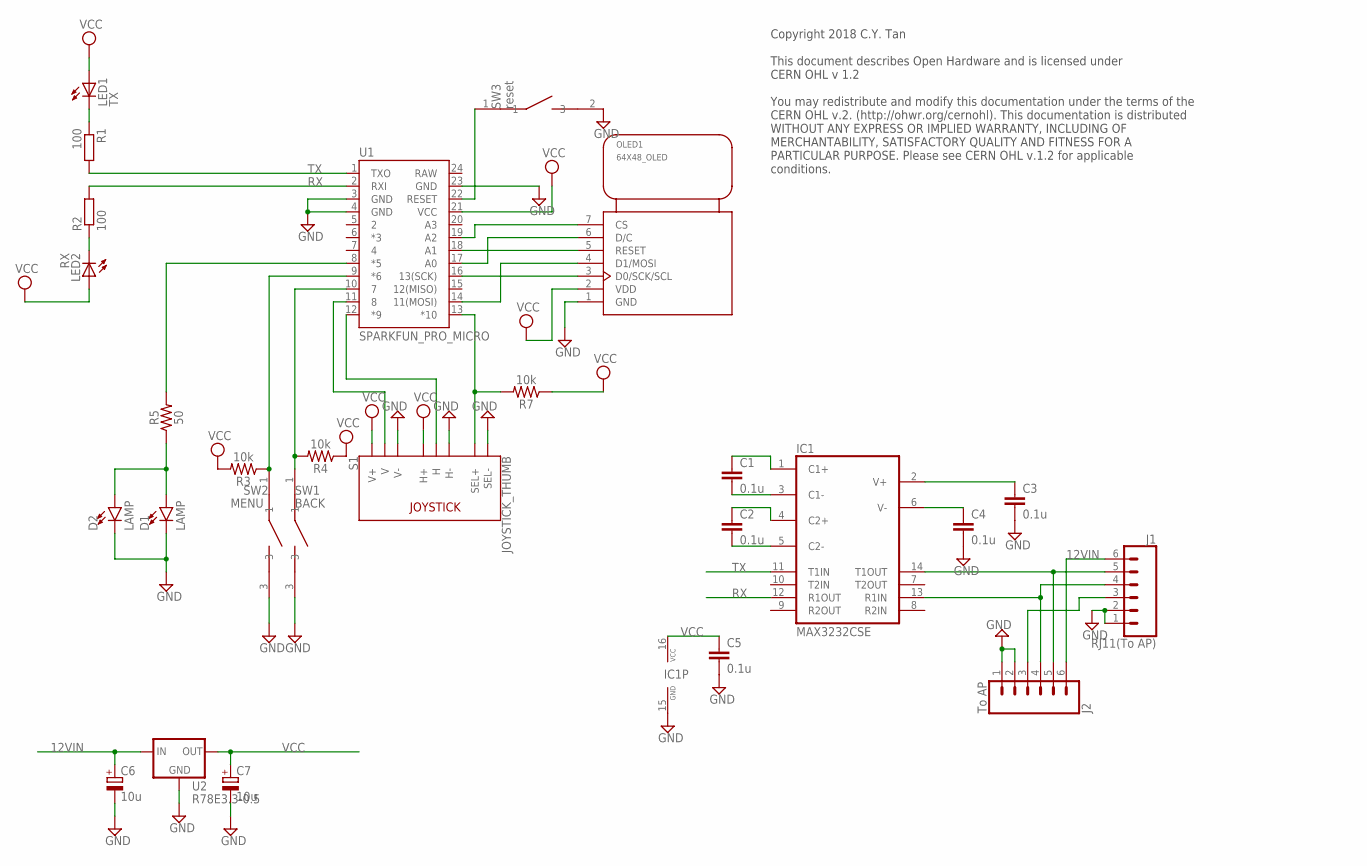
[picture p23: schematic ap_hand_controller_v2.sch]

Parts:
C1, C2, C3, C4, C5: 0.1u; C1206
C6, C7: 10u; E2,5-6
D1, D2: LAMP; LED_5MM
IC1: MAX3232CSE; SO16
J1: RJ11(To AP); RJ11-6
J2: To AP; 1X06_NO_SILK
LED1: TX; CHIPLED_1206
LED2: RX; CHIPLED_1206
OLED1: 64X48_OLED
R1, R2: 100; R0805
R3, R4, R7: 10k; AXIAL-0.3
R5: 50; AXIAL-0.3
S1: JOYSTICK_THUMB; JOYSTICK
SW1: BACK; TSA12110_TACT_SWITCH
SW2: MENU; TSA12110_TACT_SWITCH
SW3: reset; TACTILE_SWITCH_90DEG
U1: SPARKFUN_PRO_MICRO
U2: R78E3.3-0.5; DC-DC_CONVERTER_78XX

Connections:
12VIN: C6.+, J1.6, J2.6, U2.VIN (IN)
GND: C3.2, C4.2, C5.2, C6.-, C7.-, D1.K (C), D2.K (C), IC1.15 (GND), J1.1, J1.2, J2.1, J2.2, OLED1.1 (GND), S1.B2A (SEL-), S1.H3 (H-), S1.V3 (V-), SW1.3, SW2.3, SW3.2 (3), U1.3 (GND), U1.4 (GND), U1.23 (GND), U2.GND
unnamed: C1.1, IC1.1 (C1+)
unnamed: C1.2, IC1.3 (C1-)
unnamed: C2.1, IC1.4 (C2+)
unnamed: C2.2, IC1.5 (C2-)
unnamed: C4.1, IC1.6 (V-)
unnamed: C3.1, IC1.2 (V+)
unnamed: IC1.14 (T1OUT), J1.5, J2.5
unnamed: IC1.13 (R1IN), J1.4, J2.4
unnamed: LED1.C, R1.1
unnamed: LED2.C, R2.1
unnamed: S1.V2 (V), U1.11 (8)
unnamed: S1.H2 (H), U1.12 (*9)
unnamed: SW3.1, U1.22 (RESET)
unnamed: OLED1.3 (D0/SCK/SCL), U1.16 (13(SCK))
unnamed: OLED1.6 (D/C), U1.17 (A0)
unnamed: OLED1.4 (D1/MOSI), U1.14 (11(MOSI))
unnamed: OLED1.5 (RESET), U1.18 (A1)
unnamed: OLED1.7 (CS), U1.19 (A2)
unnamed: R4.P$2 (2), SW1.1, U1.10 (7)
unnamed: R3.P$1 (1), SW2.1, U1.9 (*6)
unnamed: D1.A, D2.A, R5.P$1 (1)
unnamed: R7.P$2 (2), S1.B1A (SEL+), U1.13 (*10)
unnamed: J1.3, J2.3
unnamed: R5.P$2 (2), U1.8 (*5)
RAW: U1.24 (RAW)
RX: IC1.12 (R1OUT), R2.2, U1.2 (RXI)
TX: IC1.11 (T1IN), R1.2, U1.1 (TXO)
VCC: C5.1, C7.+, IC1.16 (VCC), LED1.A, LED2.A, OLED1.2 (VDD), R3.P$2 (2), R4.P$1 (1), R7.P$1 (1), S1.H1 (H+), S1.V1 (V+), U1.21 (VCC), U2.VOUT (OUT)

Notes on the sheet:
Copyright 2018 C.Y. Tan This document describes Open Hardware and is licensed under CERN OHL v 1.2 You may redistribute and modify this documentation under the terms of the CERN OHL v.2. (http://ohwr.org/cernohl). This documentation is distributed WITHOUT ANY EXPRESS OR IMPLIED WARRANTY, INCLUDING 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

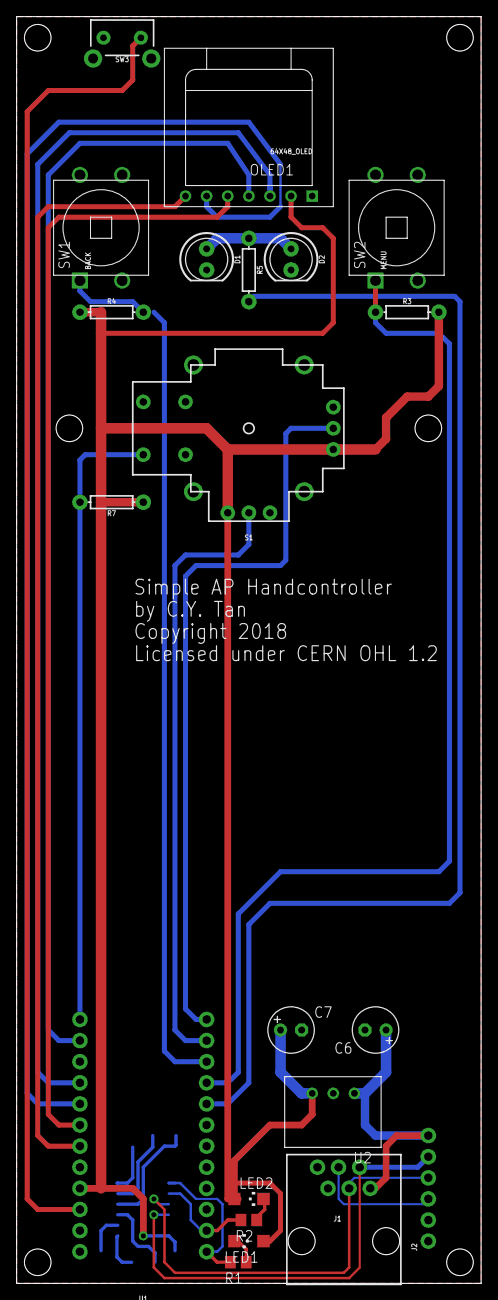
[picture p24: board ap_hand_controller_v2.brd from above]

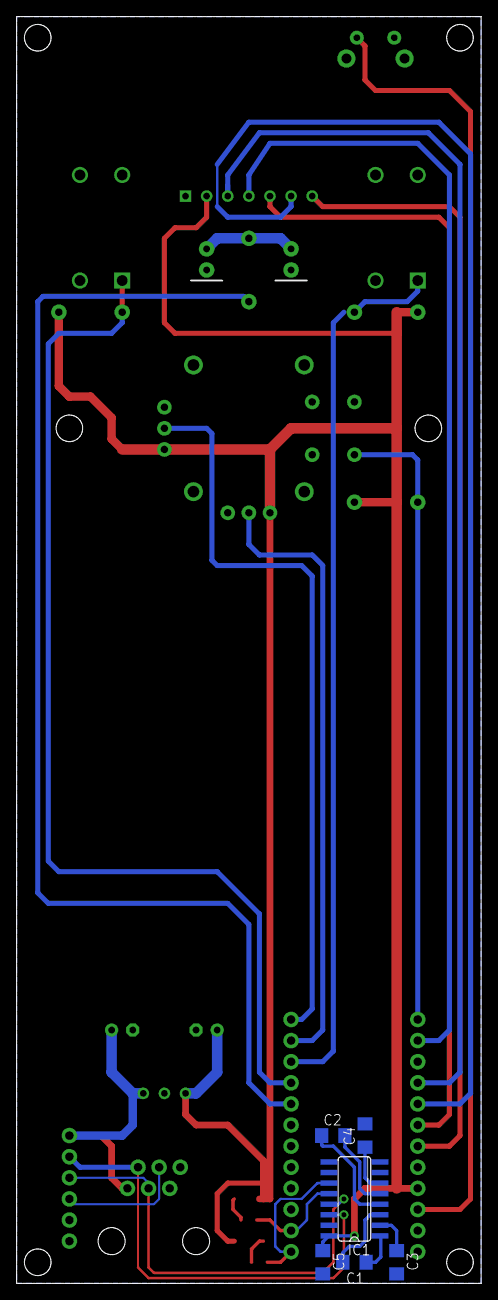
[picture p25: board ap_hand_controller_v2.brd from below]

Board: 2 copper layers, 55.9 x 152.4 mm, 27 parts (6 on the bottom side), 29 nets.

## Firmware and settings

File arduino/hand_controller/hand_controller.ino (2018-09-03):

/*$Id: hand_controller.ino | Sun Sep 2 13:58:51 2018 -0500 | cytan  $*/
/*
    hand_controller is the controller code for the Arduino Sparkfun Pro Micro
    Copyright (C) 2018  C.Y. Tan
    Contact: cytan299@yahoo.com

    This file is part of hand_controller

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
*/

/* operating system header files (use <> for make depend) */
#include <Arduino.h>
#include <string.h>

/* general system header files (use "" for make depend) */

#include <SPI.h>  
#include <SFE_MicroOLED.h>
#include <MenuSystem.h>

/* local include files (use "") */
#include "EnableInterrupt.h"

/**********************************************************************
  There are two hardware versions. The development version is Version 1
  and the release version is version 2.
  So for all users: uncomment VERSION2 if it is commented out below
 **********************************************************************/

//#define VERSION2

/**********************************************************************
  Define the pins of the OLED and make the OLED
 **********************************************************************/
#define OLED_PIN_RESET A1  
#define OLED_PIN_DC    A0  
#define OLED_PIN_CS    A2 

MicroOLED oled(OLED_PIN_RESET, OLED_PIN_DC, OLED_PIN_CS); // SPI declaration

// size of the oled
#define PIXEL_XMAX	64
#define PIXEL_YMAX	48

/**********************************************************************
  Define the pins used for the joystick and its button
 **********************************************************************/
#define JOY_RA		A8
#define JOY_DEC		A9
#define JOY_BUTTON	A10
#define JOY_BUTTON_PIN	10

/**********************************************************************
  Define the led lights pwm pin
 **********************************************************************/
#define LED_LIGHT	5

/**********************************************************************
  Define the menu and back buttons
 **********************************************************************/
#define BACK_BUTTON	6
#define MENU_BUTTON	7

/**********************************************************************
NAME

	AP - class that encapsulates the commands to control the AP mount
		   
SYNOPSIS
	
	AP is the class that encapsulates the commands to control the
	AP mount using serial commands given in the protocol-G.pdf
	manual. Only the necessary commands for this handcontroller
	are implemented.

INTERFACE
	ClearBuffer()	- Tell GTOCP4 to clear its buffer
	IsConnected()	- Returns true if the handcontroller is
		          connected to the GTOCP4 and a valid version
			  is returned. Doesn't work with control boxes
			  with software versions earlier than B.
	GetVersion(	- Get the version of the GTOCP4
		v	- version string sent back here. v is an int array.
	)		- returns false if no version string is
			  returned
	SendSlewRate(	- send the slew rate to the GTOCP4
		v	- to this value. Note: NO CHECKS are done at
			  this time. 
	)
	IncrementSlewRate() - increment the slew rate according to the
			      values in _SLEW_RATES[]. Slew rate will
			      wrap around when it gets to the end of
	                      the _SLEW_RATES[] array.
			      Returns the value of the slew rate.
			      NOTE: Nothing gets sent to the GTOCP4
			      until SendSlewRate() is called.
			      
	DecrementSlewRate() - decrement the slew rate according to the
			      values in _SLEW_RATES[]. Slew rate will
			      wrap around when it gets to the start of
	                      the _SLEW_RATES[] array.
			      Returns the value of the slew rate.
			      NOTE: Nothing gets sent to the GTOCP4
			      until SendSlewRate() is called.

	SetSlewRateI(	- Set the slew rate to this _SLEW_RATES[]	
		i	- index value	
	)		- NO CHECKS ARE DONE! and nothing getssent
		          to the GTOCP4 until SendSlewRate() is called.
	GetSlewRate()	- returns the current slew rate.
	GetSlewRateI()	- returns the current slew rate index of
			  _SLEW_RATES[]
	SetAndSendSlewRateI( -Set the slew rate to this _SLEW_RATES[]	
		i	     - index value and send it to the GTOCP4.	
	)
	GetSlewRateName(  - return the name of the slew rate	
		i	  - for this index in _SLEW_RATE_NAMES[]
	)
	Move(		- Move the telescope in the direction
	  d		- given by d
	)		- Slew rate has been set previously with the
			  *SlewRate*() functions.
	GetDirection()	- return the direction that the telescope is
			  slewing.
	SetHome()	- set the home position of the telescope.
			  Returns 0 on success
				 -1: cannot set ALT
				 -2: cannot set AZ
	GoHome()	- Tell telescope to go to previously set HOME
			  position.
			  Returns 0 on success
				 -1: send ALT failed
				 -2: send AZ failed
				 -3: GTOCP4 go home failed
				 -4: No HOME value set

	IsHomeSet()	- returns true if HOME has been set
	IsHome()	- returns true if the telescope is at HOME
			  position.
	Park()		- park the telescope at this current position.


PRIVATE FUNCTIONS
	send(		- send
	   cmd		  this command string to the GTOCP4	
	)		- returns 0 on success

	receive(	- receive the 
	   data		  data from the GTOCP4
	   stop		  The stop character. Default: "#"
	)		- returns the size of the data array.
			  -1 on failure. receive() does not wait
			  forever. It will fail after some time and
			  returns -1.
	
AUTHOR
	C.Y. Tan

SEE ALSO
	protocol-G.pdf

**********************************************************************/

enum DIRECTION {NORTH, NORTH_EAST, NORTH_WEST,
		SOUTH, SOUTH_EAST, SOUTH_WEST,
		EAST, WEST,
		STOP, FORCE_STOP};

class AP
{
public:
  AP();
public:
  void ClearBuffer();
  bool IsConnected();
  bool GetVersion(int* v);

  void SendSlewRate(const int s);
  int IncrementSlewRate();
  int DecrementSlewRate();
  void SetSlewRateI(const int i);
  int GetSlewRate() const;
  int GetSlewRateI() const;
  void SetAndSendSlewRateI(const int i);
  char* GetSlewRateName() const;
  void Move(DIRECTION d);
  DIRECTION GetDirection() const;
  int SetHome();
  int GoHome();
  bool IsHomeSet();
  bool IsHome();
  void Park();

public:
  static char* _SLEW_RATE_NAMES[];  
  
private:
  int send(const __FlashStringHelper*cmd) const;
  int receive(int* const data, int stop='#') const;

  int _slew_rate_i;
  int _max_slew_rate_i;
  static int _SLEW_RATES[];

  DIRECTION _dir;

  bool _is_home_set;
  char _alt[32];
  char _az[32];

  
};

/*
    _SLEW_RATES[] values:
	0: 12x
	1: 64x
	2: 600x
	3: 1200x
*/
int AP::_SLEW_RATES[] = {0, 1, 2, 3};

char* AP::_SLEW_RATE_NAMES[] = {"Fine_12x",
				"Slow_64x",
				"Med_600x",
				"Fast_1200x"};

AP::AP()
{
  _slew_rate_i = 2; // default slew rate is 600x
  _max_slew_rate_i = 4;//sizeof(_SLEW_RATES)/sizeof(int);
  _dir = STOP;

  _is_home_set = false;
  _alt[0] ='\0';
  _az[0] = '\0';
}
void AP::ClearBuffer()
{
  send(F("##"));
}

bool AP::IsConnected()
{
  if(Serial1){
    //check version of the control box
    int buf[16];
    return GetVersion(buf);
  }
  else {
    return false;
  }
}

bool AP::GetVersion(int* v)
{
  send(F("#:V#"));
  int len = receive(v);
  if(len > 0){
    if(v[len-1] == '#'){
      return true;
    }
    else return false;
  }
  else return false;
}

void AP::SendSlewRate(const int v)
{
  // Use centering rate :RCxxx# rather than slew rate :RSxxx#
  // The reason is that :RCxxx# is what the handcontroller will use
  // while the :RSxxx# will be used by the ASCOM driver.
  if(Serial1){
    Serial1.print("#:RC");
    Serial1.print(v, DEC);
    Serial1.println("#");
    Serial1.flush();
  }
}

int AP::IncrementSlewRate()
{
  _slew_rate_i++;
  if(_slew_rate_i >= _max_slew_rate_i){
    // wrap around
    _slew_rate_i = 0;
  }
  return _SLEW_RATES[_slew_rate_i];
}

int AP::DecrementSlewRate()
{
  _slew_rate_i--;
  if(_slew_rate_i < 0){
    // wrap around
    _slew_rate_i = _max_slew_rate_i-1;
  }
  return _SLEW_RATES[_slew_rate_i];
}

void AP::SetSlewRateI(const int i)
{
  _slew_rate_i = i;
}

int AP::GetSlewRate() const
{
  return _SLEW_RATES[_slew_rate_i];
}

int AP::GetSlewRateI() const
{
  return _slew_rate_i;
}

void AP::SetAndSendSlewRateI(const int i)
{
  _slew_rate_i = i;
  SendSlewRate(_SLEW_RATES[_slew_rate_i]);
}

char* AP::GetSlewRateName() const
{
  return _SLEW_RATE_NAMES[_slew_rate_i];
}
   

void AP::Move(DIRECTION d){

  if(d == FORCE_STOP){
    send(F("#:Q#")); // FORCE a STOP!!!!
    _dir=FORCE_STOP;

    return;
  }
  
  // move until stop is issued.
  switch (d) {
    case NORTH:
      if(_dir != NORTH){
	send(F("#:Q#")); // stop the previous direction
        send(F("#:Mn#"));
	_dir = NORTH;
      } // don't do anything if we are already moving north
      break;
    case SOUTH:
      if(_dir != SOUTH){
        send(F("#:Q#")); // stop the previous direction	
        send(F("#:Ms#"));
	_dir = SOUTH;
      }
      break;
    case EAST :
      if(_dir != EAST){
        send(F("#:Q#")); // stop the previous direction
        send(F("#:Me#"));
	_dir = EAST;
      }
      break;
    case WEST :
      if(_dir != WEST){
	send(F("#:Q#")); // stop the previous direction
        send(F("#:Mw#"));
	_dir = WEST;
      }
      break;
    case NORTH_EAST:
      if(_dir != NORTH_EAST){
	send(F("#:Q#")); // stop the previous direction
        send(F("#:Mn#"));
        send(F("#:Me#"));	
	_dir = NORTH_EAST;
      } 
      break;
    case NORTH_WEST:
      if(_dir != NORTH_WEST){
	send(F("#:Q#")); // stop the previous direction
        send(F("#:Mn#"));
        send(F("#:Mw#"));	
	_dir = NORTH_WEST;
      } 
      break;
    case SOUTH_EAST:
      if(_dir != SOUTH_EAST){
	send(F("#:Q#")); // stop the previous direction
        send(F("#:Ms#"));
        send(F("#:Me#"));	
	_dir = SOUTH_EAST;
      } 
      break;
    case SOUTH_WEST:
      if(_dir != SOUTH_WEST){
	send(F("#:Q#")); // stop the previous direction
        send(F("#:Ms#"));
        send(F("#:Mw#"));	
	_dir = SOUTH_WEST;
      } 
      break;            
    case STOP :
      if(_dir != STOP){
	send(F("#:Q#")); // stop moving!
	_dir = STOP;
      }
      break;
  }
}

DIRECTION AP::GetDirection() const
{
  return _dir;
}

int AP::SetHome()
{
  int data[32];
  int len;

  _is_home_set = false;
  
  send(F("#:GA#")); // get alt
  if((len=receive(data)) > 0){
    for(int i=0; i<len; i++){
      _alt[i] = (char)data[i];
    }
    _alt[len] = '\0';    
  }
  else {
    return -1;
  }

  send(F("#:GZ#")); // get az
  if((len=receive(data)) > 0){
    for(int i=0; i<len; i++){
      _az[i] = (char)data[i];
    }
    _az[len] = '\0';
  }
  else {
    return -2;
  }
#ifdef AAAAA
  Serial.print("alt"); Serial.println(_alt);
  Serial.print("az"); Serial.println(_az);
#endif
  _is_home_set = true;
  return 0;  
}

int AP::GoHome()
{
  if(_is_home_set){
    int data[32];
  
    //  :Sa sDD*MM# or :Sa sDD*MM:SS#
    
    if(Serial1){
      // send alt
      Serial1.print(F("#:Sa "));
      Serial1.println(_alt); // alt already contains a '#' at the end
      Serial1.flush();    
      // wait 1
      if(receive(data, '1') > 0){
	if(data[0] != '1'){
	  return -1;
	}
      }
      else {
        return -1;
      }
  

      //:Sz DDD*MM# or :Sz DDD*MM:SS#    
      Serial1.print(F("#:Sz "));
      Serial1.println(_az); // az already contains a '#' at the end
      Serial1.flush();

      // wait 1
      if(receive(data, '1') > 0){
        if(data[0] != '1'){
          return -2;
        }
      }
      else {
        return -2;
      }

      // go home
      send(F("#:MS#"));
      if(receive(data, '0') > 0){
	if(data[0] != '0'){
          return -3;
	}
      }
    } // Serial1
  } // is_home_set
  else {
    return -4;
  }
  return 0;  
}

bool AP::IsHomeSet()
{
  return _is_home_set;
}

bool AP::IsHome()
{
  int data[32];
  int len;
  
  send(F("#:GA#")); // get alt
  if((len=receive(data)) > 0){
    if(strlen(_alt) == len){
      for(int i=0; i<len; i++){
        if(_alt[i] != (char)data[i]){
	  return false;
        }
      }
    }
    else {
      return false;
    }
  }
  else {
    return false;
  }

  send(F("#:GZ#")); // get az
  if((len=receive(data)) > 0){
    if(strlen(_az) == len){
      for(int i=0; i<len; i++){
	if(_az[i] != (char)data[i]){
	  return false;
	}
      }
    }
    else {
      return false;
    }
  }
  else {
    return false;
  }

  return true;    
}

void AP::Park()
{
  send(F("#:KA#"));
}

int AP::send(const __FlashStringHelper*cmd) const
{
  if(Serial1){
    Serial1.println(cmd);
    Serial1.flush();
  }
  else {
    return -1;
  }
  return 0;
}
  
int AP::receive(int* const data, int stop) const
{
  if(!Serial1)
    return -1;
    
  int* pdata = data;
  int len = 0;
  const long wait_limit = 1000000;
  long wait_i = 0;
#ifdef AAAAAAA
    Serial.print("Received: ");
#endif
  bool is_done = false;
  while(!is_done && wait_i < wait_limit){
  int num_bytes;
  if((num_bytes=Serial1.available()) > 0){
    wait_i = 0; // reset wait
      
    len += num_bytes;
    for(int i=0; i<num_bytes; i++){
      int ch = Serial1.read();
      *pdata++ = ch;
      // write the char
#ifdef AAAAAA	
	  Serial.write(ch);
#endif	
      if(ch == stop)
	is_done = true;
      }
    }
    else {
      wait_i++;
    }
  }
#ifdef AAAAAA    
    Serial.println("");
    Serial.print("wait_i=");
    Serial.println(wait_i, DEC);
#endif  
  return wait_i >= wait_limit? -1: len;    
}

AP ap;

/**********************************************************************
NAME

	JoyStick - class that encapsulates the behaviour of the joystick
		   
SYNOPSIS
	
	JoyStick allows the user to query the joystick as a 4 position
	switch or to return its value that is mapped from -512 to
	+512.

INTERFACE
	
	GetDecState()	- returns JOY_UP, JOY_DOWN or JOY_CENTRED
	GetRAState()	- returns JOY_LEFT, JOY_RIGHT or JOY_CENTRED
	IsClicked()	- returns true if the joystick button is
			  clicked
	GetR()		- returns the radial position of the
			  joystick. 
	
AUTHOR
	C.Y. Tan

SEE ALSO

**********************************************************************/
volatile bool is_joy_pressed = false;

void joy_state_int()
{
  is_joy_pressed = true;
}

enum JOY_STATE { JOY_CENTRED, JOY_DOWN, JOY_UP, JOY_LEFT, JOY_RIGHT};

#define DEBOUNCE_TIME	50 // ms
class JoyStick {
private:
  unsigned long _last_DEC_debounce_time = 0; // ms
  JOY_STATE _last_DEC_state = JOY_CENTRED;

  unsigned long _last_RA_debounce_time = 0; // ms
  JOY_STATE _last_RA_state = JOY_CENTRED;  
  
public:
  JoyStick(){
    // set up joystick button as interrupt
    pinMode(JOY_BUTTON, INPUT_PULLUP);
    enableInterrupt(JOY_BUTTON_PIN, joy_state_int, FALLING);
  }
  
  JOY_STATE GetDecState() {
    // read the joystick dec
    int dec = analogRead(JOY_DEC);
    JOY_STATE state;
    // 500 in middle. Up is 0, down is 1024    
    if(dec < 480){
      state = JOY_UP;
    }
    else {
      if(dec > 544){
	state = JOY_DOWN;
      }
      else {
	state = JOY_CENTRED;
      }
    }

    if(state != _last_DEC_state){
      // check whether it is greater than debounce time
      unsigned long now = millis();
      if((now - _last_DEC_debounce_time) > DEBOUNCE_TIME){
        // now the state really has really changed!
	_last_DEC_debounce_time = now;	
	_last_DEC_state = state;
      }
    }

    return _last_DEC_state;
  }

  JOY_STATE GetRAState() {
    // read the joystick ra
    int ra = analogRead(JOY_RA);
    JOY_STATE state;
    // 500 in middle. right is 0, left is 1024    
    if(ra < 480){
      state = JOY_RIGHT;
    }
    else {
      if(ra > 544){
	state = JOY_LEFT;
      }
      else {
	state = JOY_CENTRED;
      }
    }

    if(state != _last_RA_state){
      // check whether it is greater than debounce time
      unsigned long now = millis();
      if((now - _last_RA_debounce_time) > DEBOUNCE_TIME){
        // now the state really has really changed!
	_last_RA_debounce_time = now;	
	_last_RA_state = state;
      }
    }

    return _last_RA_state;
  }

  bool IsClicked() const{
    if(is_joy_pressed){
      is_joy_pressed = false;
      return true;
    }
    return false;
  }

  int GetR() const{
    float ra = static_cast<float>(analogRead(JOY_RA) - 512);
    float dec = static_cast<float>(analogRead(JOY_DEC) - 512);
#ifdef AAAAA
    Serial.print("("); Serial.print(ra, DEC); Serial.print(",");
    Serial.print(dec, DEC); Serial.println(")");
#endif
    return static_cast<int>(sqrt(ra*ra + dec*dec));
  }
};

JoyStick joy_stick;

/**********************************************************************
NAME

	MenuBackButtons - class that encapsulates the behaviour of the
	two buttons that the user can push
		   
SYNOPSIS
	
	MenuBackButtons is a class that encapsulates the behaviour of
	the two buttons that the user can push. They are the MENU
	button and the BACK button

INTEFACE
	GetState() - returns MENU_ON, BACK_ON or BOTH_OFF	
	
AUTHOR
	C.Y. Tan

SEE ALSO

**********************************************************************/

enum BUTTON_STATE {MENU_ON, BACK_ON, BOTH_OFF};

class MenuBackButtons {
public:
  MenuBackButtons(){
    //set up the menu and back buttons
    pinMode(MENU_BUTTON, INPUT);
    digitalWrite(MENU_BUTTON, HIGH);

    pinMode(BACK_BUTTON, INPUT);
    digitalWrite(BACK_BUTTON, HIGH);      
  }

  BUTTON_STATE GetState() const {
    // not doing any debouncing here. Seems to work.
    if(digitalRead(MENU_BUTTON) == 0){
      return MENU_ON;
    }

    if(digitalRead(BACK_BUTTON) == 0){
      return BACK_ON;
    }

    return BOTH_OFF;
  }

};

MenuBackButtons mb_buttons;


/**********************************************************************
NAME

	LEDLight - class that controls the brightness of the LED lights

		   
SYNOPSIS
	
	LEDLight class controls the brightness of the LED lights

INTERFACE
	Increase()	- increase the brightness of the LED lights
	Decrease()	- decrease the brightness of the LED lights
	
AUTHOR
	C.Y. Tan

SEE ALSO

**********************************************************************/

class LEDLight
{
public:
  LEDLight(){
    // setup PWM for the led light
    pinMode(LED_LIGHT, OUTPUT);
    _level = 0x80;
    analogWrite(LED_LIGHT, _level);
  }

  void Increase(){
    if(_level+4 < 255){
      _level+= 4;
    }
    else {
      _level = 255;
    }
    analogWrite(LED_LIGHT, _level);
  }

  void Decrease(){
    unsigned char level = _level;
    if(_level - 4 > 0){
      _level -= 4;
    }
    else {
      _level = 0;
    }
    analogWrite(LED_LIGHT, _level);    
  }

  unsigned char GetLevel() const
  {
    return _level;
  }

private:
  int _level;
};

LEDLight led;

/**********************************************************************
NAME

	HCRenderer - the handcontroller OLED renderer for menu items
		   
SYNOPSIS
	
	HCRenderer is the class for rendering menu items of the
	OLED. This is a required class for the MenuSystem

INTERFACE
	The following functions have to be defined so that the base
	class MenuComponentRenderer's virtual functions
	render()	- defines how the menu is rendered on the OLED

	render_menu_item(), render_back_menu_item(),
	render_numeric_menu_item() and render_menu() are all functions
	that render the menu on the OLED display

	
AUTHOR
	C.Y. Tan

SEE ALSO

**********************************************************************/

// font 0 is 5x7
#define FONT_H 7 // font height
#define LINE_SPACE 4 // spacing between lines
#define SELECT_SPACE 2 // spacing below the font for select line

class HCRenderer: public MenuComponentRenderer{
public:
  void render(Menu const& menu) const {
    oled.clear(PAGE); // clear the buffer
    oled.setCursor(0,0);
    oled.print(menu.get_name());
    oled.display();	    

    for(int i=0; i<menu.get_num_components(); i++){
      MenuComponent const* cp = menu.get_menu_component(i);
      
      oled.setCursor(0, (i+1)*(FONT_H+LINE_SPACE));
      
      if(cp != NULL){
	cp->render(*this);
	if(cp->is_current()){
	  oled.line(0, (i+1)*(FONT_H+LINE_SPACE) + (FONT_H+SELECT_SPACE),
		    PIXEL_XMAX, (i+1)*(FONT_H+LINE_SPACE) + (FONT_H+SELECT_SPACE));	  
	  oled.display();
	}
      }
      else {
      }
    }
  }

  void render_menu_item(MenuItem const& menu_item) const {
    oled.print(menu_item.get_name());
    oled.display();    
  }

  void render_back_menu_item(BackMenuItem const& menu_item) const {
    oled.print(menu_item.get_name());
    oled.display();    
  }

  void render_numeric_menu_item(NumericMenuItem const& menu_item) const {
    oled.print(menu_item.get_name());
    oled.display();    
  }

  void render_menu(Menu const& menu) const {
    oled.print(menu.get_name());
    oled.display();    
  }
};

/**********************************************************************
  Define the menu items
 **********************************************************************/

HCRenderer hc_renderer;

// Forward declarations

void on_nav_selected(MenuComponent*);
void on_rate_selected(MenuComponent*);
void on_ra_move_selected(MenuComponent*);
void on_prop_nav_selected(MenuComponent*);
void on_sethome_selected(MenuComponent*);
void on_gohome_selected(MenuComponent*);
void on_led_selected (MenuComponent*);

// Menu variables

MenuSystem ms(hc_renderer);
  Menu mn_nav("Navigation");
    MenuItem mi_nav("Navigate", &on_nav_selected);
    MenuItem mi_rate(ap.GetSlewRateName(), &on_rate_selected);
    MenuItem mi_prop_nav("Prop Nav", &on_prop_nav_selected);
  Menu mn_pm("PoleMaster");
    MenuItem mi_sethome("Set home", &on_sethome_selected);
    MenuItem mi_ra("RA move", &on_ra_move_selected);
    MenuItem mi_gohome("Go home", &on_gohome_selected);
  MenuItem mi_led("LED lights", &on_led_selected);



/**********************************************************************
TITLE

  The menu callbacks and helper functions
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
void loop()
{
  /*
    I have to wait for awhile (150 ms) after selecting a menu item, so
    that there is time for the item to be highlighted and not go
    immediately to the next menu item.
   */
  delay(150);  
  process_menu();
}

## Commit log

2018-07-29 A simple handcontroller for Astro-Physics mounts
    [ap_hand_controller_v2.brd, ap_hand_controller_v2.sch, bom.ods]
2018-07-29 Updated arduino/hand_controller
2018-07-29 First try to fix arduino/hand_controller access problem by removing it
2018-07-29 Hopefully now arduino/hand_controller is accessible
2018-07-29 removed arduino/hand_controller
2018-07-29 removed arduino subdirectory
2018-07-29 Re-added arduino subdirectory
2018-07-29 Removed arduino/hand_controller again
2018-07-30 Added README.md to bom directory
2018-08-12 Updated arduino/handcontroller code to swap East and West keys so that behaviour is in the usual convention
    [hand_controller.ino]
2018-08-16 bom: updated bill of materials
    [bom.ods]
2018-09-02 arduino: Major improvement. Joystick pushbutton now uses an interrupt to make response time faster.
2018-09-02 arduino: improved responsiveness of joystick of handcontroller.
2021-01-07 bom.ods: Updated components without Digikey part numbers.
    [bom.ods]
2021-03-28 Fixed Vcc unconnected bug in ap_hand_controller_v2.brd. Thanks to Andrew (ab15Kath) for discovering this bug.
    [ap_hand_controller_v2.brd]
2025-07-31 bom/updated link for OLED source
    [bom.ods]
2025-08-01 bom/bom.ods updated link to where to purchase OLED
    [bom.ods]

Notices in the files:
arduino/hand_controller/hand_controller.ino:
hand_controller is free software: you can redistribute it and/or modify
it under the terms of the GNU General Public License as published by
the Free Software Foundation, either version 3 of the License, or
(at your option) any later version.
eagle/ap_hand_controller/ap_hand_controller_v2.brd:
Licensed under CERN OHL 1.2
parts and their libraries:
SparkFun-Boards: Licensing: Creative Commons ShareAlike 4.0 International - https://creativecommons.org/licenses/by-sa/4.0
